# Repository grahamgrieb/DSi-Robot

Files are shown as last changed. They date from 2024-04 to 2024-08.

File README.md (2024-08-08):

#### This project uses a Nintendo DSi to control a worm-like origami robot. The  DSi also streams live video data from its webcam to a TFT Display on the robot. This project involved programming custom homebrew, designing a PCB cartridge for the DSi, wireless ESP to ESP communication, image encoding, and motor control. Both the robot and DSi operate completely wirelessly.
| *The robot and the DSi with its custom cartridge slotted in* |
|:--:|
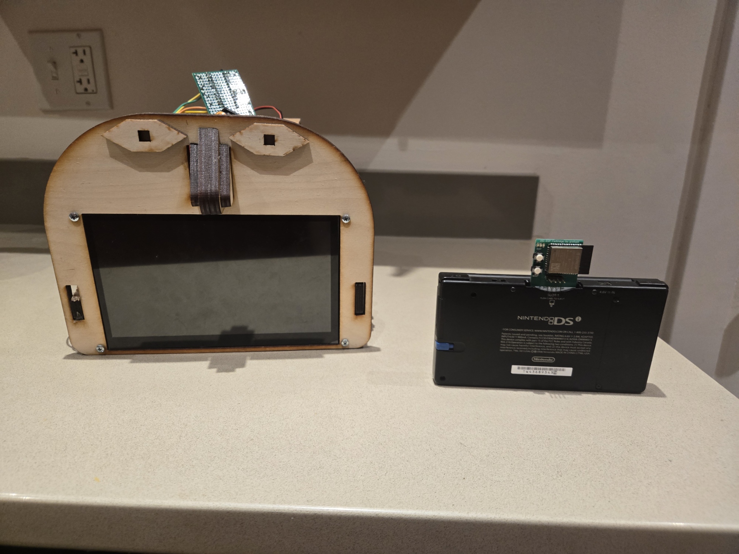
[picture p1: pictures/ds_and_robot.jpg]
Photo of DSi and Robot
|  |

| *Block Diagram overview of all the devices in the system* |
|:--:|
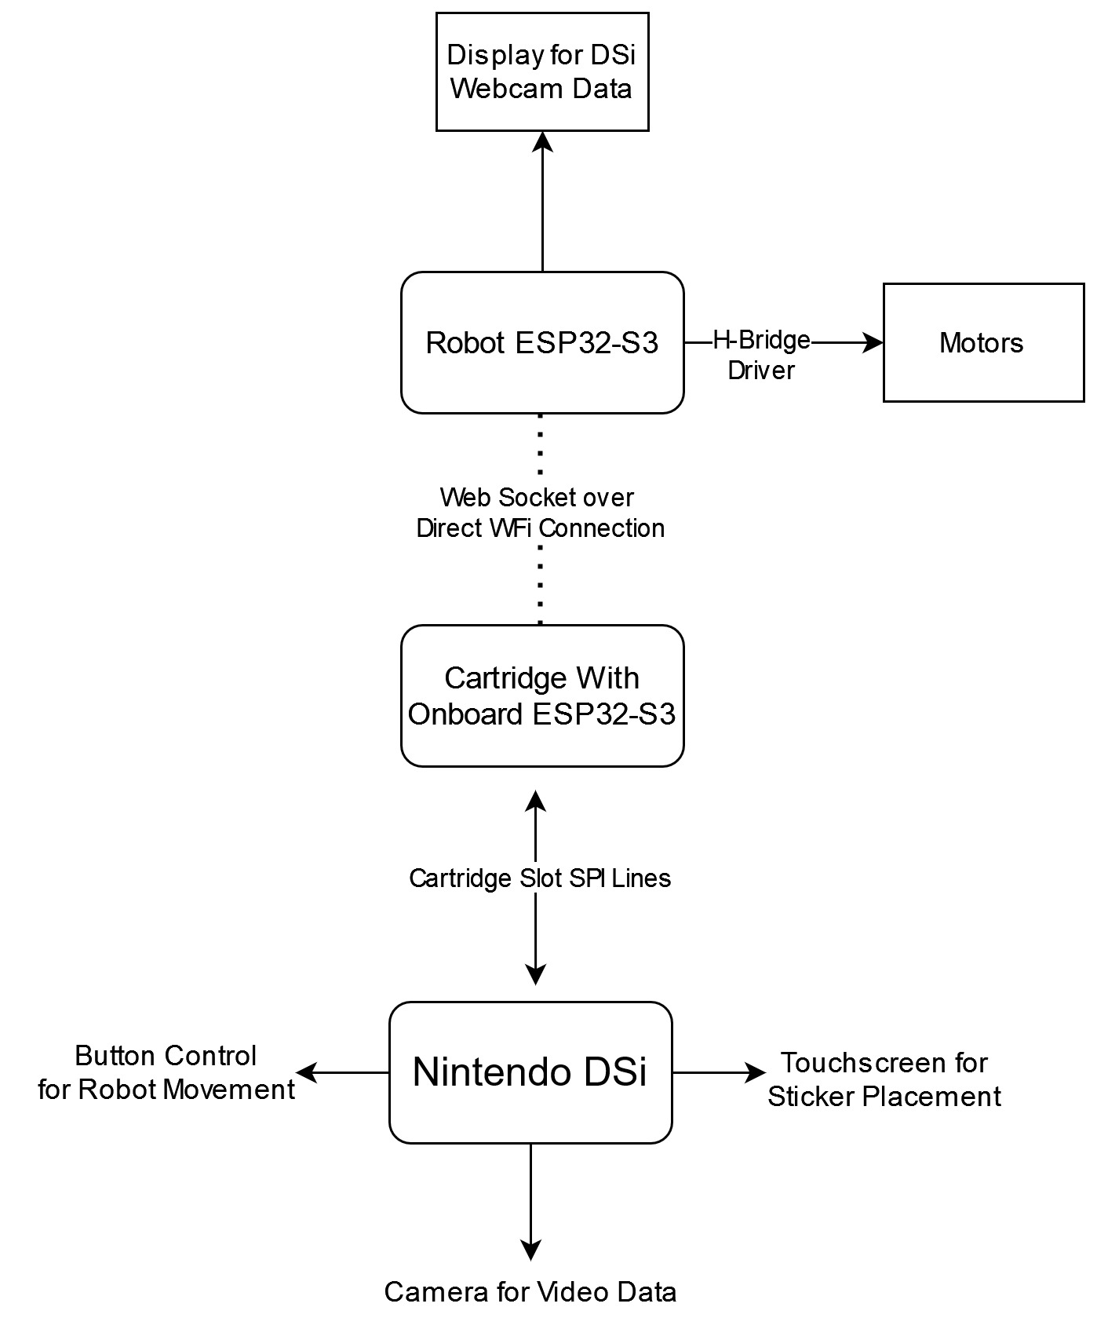
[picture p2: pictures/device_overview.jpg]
Device Block Diagram
|  |

The first part of this project is the Nintendo DSi. The DSi is running handwritten homebrew code (can be found in the **ds-app** folder). This application display the current DSi webcam data on the top screen. The user is able to place stickers over the webcam footage using the touchscreen. They are also able to switch between the front and back camera of the DSi. The webcam data is sent automatically if the user is in video mode, or whenever the user hits the A button when they are in photo mode. 

| *DSi Application with all the Stickers Placed* |
|:--:|
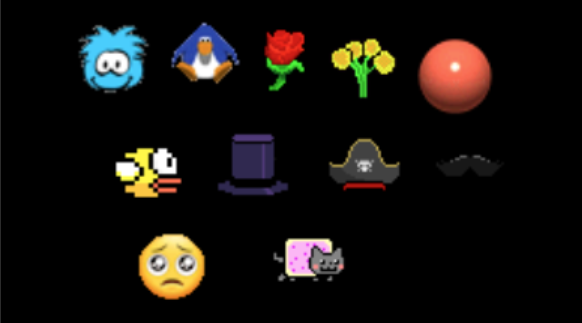
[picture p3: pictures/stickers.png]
DSi App
|  |

This application takes advantage of the two CPU's on the DSi. The image data is sent out over the SPI lines in the cartridge slot. The ARM9 CPU takes care of the main application, while the ARM7 CPU sends the SPI data in the background. These CPU's communicate with each other using the IPC register.

| *Close up of custom DSi Cartridge PCB and screenshots of Gerber files.* |
|:--:|
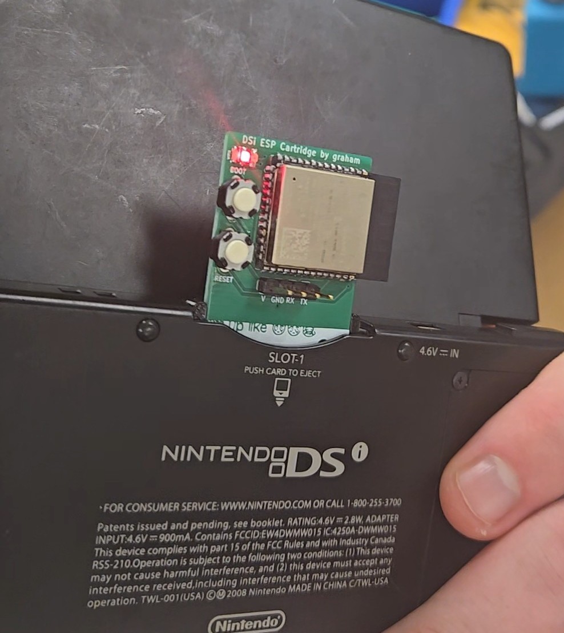
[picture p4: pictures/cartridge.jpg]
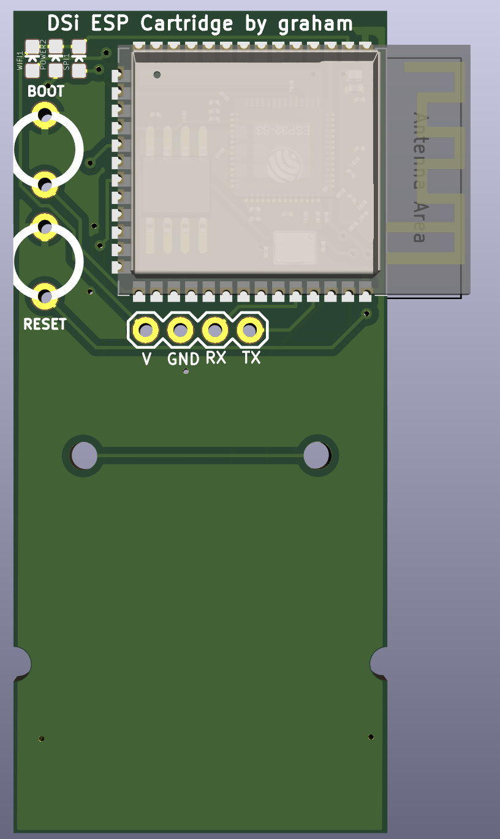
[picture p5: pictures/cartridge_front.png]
Front of Gerber
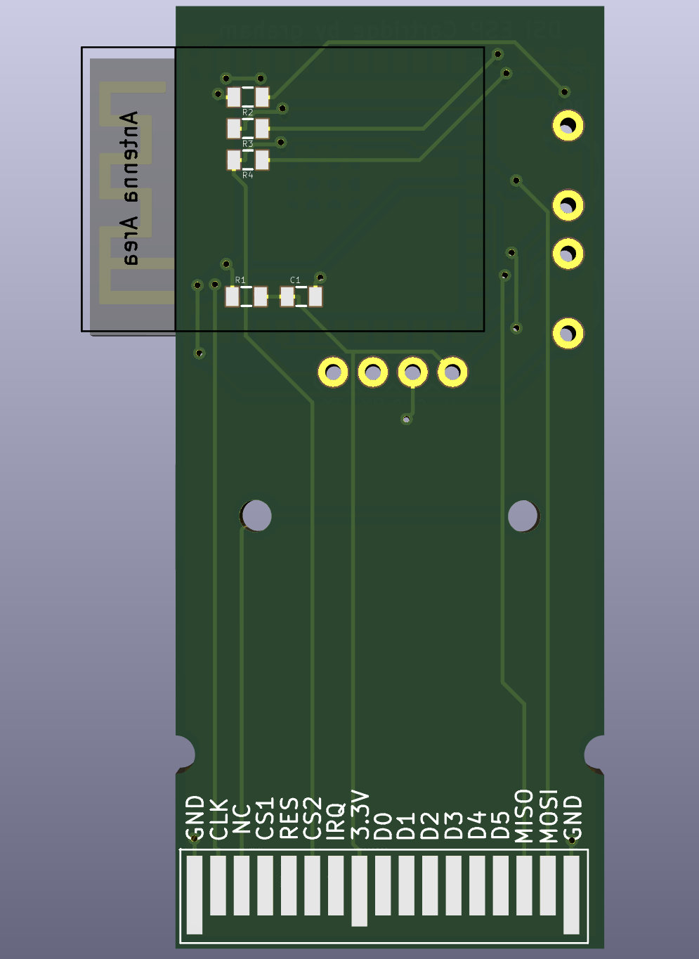
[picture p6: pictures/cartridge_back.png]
Back of Gerber
|     |

The raw bitmap image data is received over SPI on the ESP32-S3 on our custom cartridge PCB. This ESP32 is setup as SPI peripheral. It encodes the image as a JPEG (to reduce its size) and then sends it out over a WiFi WebSocket. It also receives and sends out the movement cortol signals for the robot. The code for this section can be found in **esp32-sender** folder.

The 7" TFT DIS08070H TFT Display is also powered by an ESP32-S3. The display ESP32 receives the data from the cartridge ESP32 over the direct Wifi connection. When it receives image data, it immediately draws it to the display. When it receives movement control signals, its uses our H-Bridge to appropiately tell the motors how to move. The code for this section can be found in **esp32-receiver** folder.

| *Side View of Robot* |
|:--:|
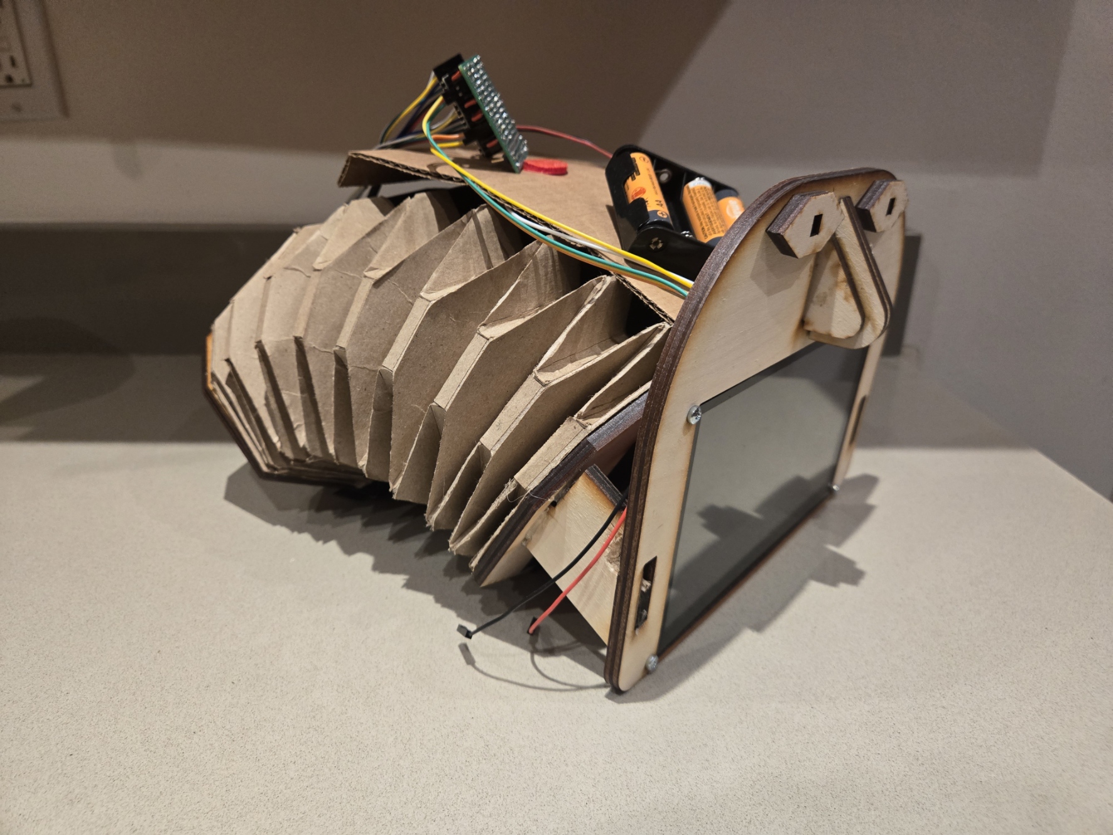
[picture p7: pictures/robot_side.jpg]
Side View of Robot
|  |

 For the robot, the design was inspired by a metamaterial soft snake robot built by the University of Southern Denmark. This design uses a Yoshimura Crease Pattern. 

The files for the cartridge PCB can be found in the **cartridge_pcb** folder and the CAD files for the cartridge housing in the **cartridge_cad** folder. The laser cutting and CAD files for the worm robot can be found in the **robot** folder.

| *Flowchart of the software/algorithm design* |
|:--:|
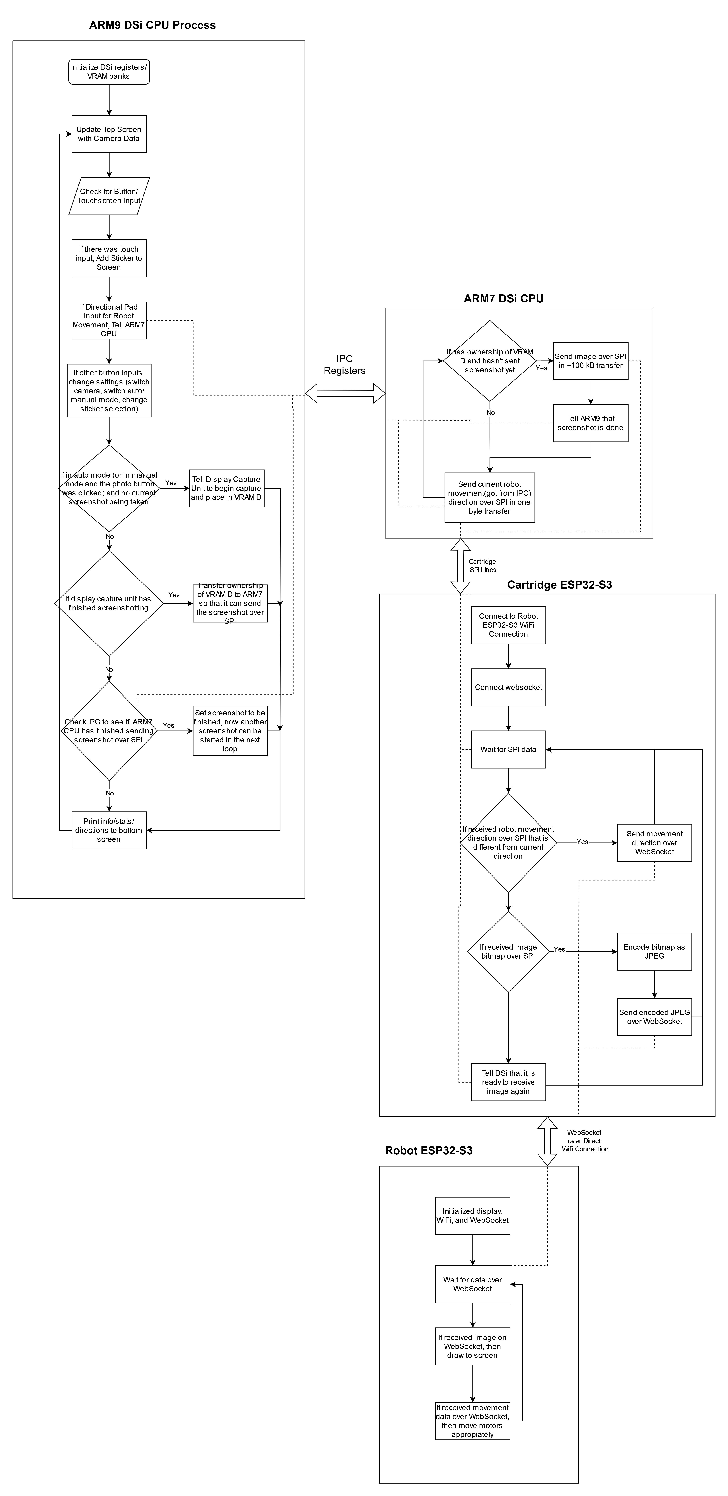
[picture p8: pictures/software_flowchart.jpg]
Software Flowchart
|  |

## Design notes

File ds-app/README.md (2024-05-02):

A homebrew application for the Nintendo DSi. Allows the user to place stickers over a live-view of the camera and save photos. Use the left and right button to change what sticker you are placing. Use b button to switch cameras.

Run make in home directory to build the program. Program cannot be run on any DSi emulators as they do not emulate the camera. devkitpro must be installed in order to build the program. The libcamera library(https://github.com/FTC55/libcamera) must also be in a parent directory to be able to build. An already built .nds file is included in the repository, this is the file that is loaded onto the DS and run.

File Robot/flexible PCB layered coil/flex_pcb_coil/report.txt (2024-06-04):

Info: Processing symbol 'J1:Connector_PinHeader_2.54mm:PinHeader_1x02_P2.54mm_Vertical'.
Added J1 (footprint 'Connector_PinHeader_2.54mm:PinHeader_1x02_P2.54mm_Vertical').
Changed REF** reference designator to J1.
Changed J1 value from PinHeader_1x02_P2.54mm_Vertical to Conn_01x02.
Updated J1 symbol association from  to /636ee8de-5b70-4620-9619-cd7a34cb071d.
Updated J1 properties.
Add net Net-(J1-Pin_1).
Connected J1 pin 1 to Net-(J1-Pin_1).
Connected J1 pin 2 to Net-(J1-Pin_1).
Warning: Via connected to unknown net ().
Warning: Via connected to unknown net ().
Warning: Via connected to unknown net ().
Warning: Via connected to unknown net ().
Warning: Via connected to unknown net ().
Warning: Via connected to unknown net ().
Warning: Via connected to unknown net ().
Warning: Via connected to unknown net ().
Warning: Via connected to unknown net ().
Warning: Via connected to unknown net ().
Warning: Via connected to unknown net ().
Warning: Via connected to unknown net ().
Warning: Via connected to unknown net ().
Warning: Via connected to unknown net ().
Warning: Via connected to unknown net ().
Warning: Via connected to unknown net ().

Info: Total warnings: 16, errors: 0.

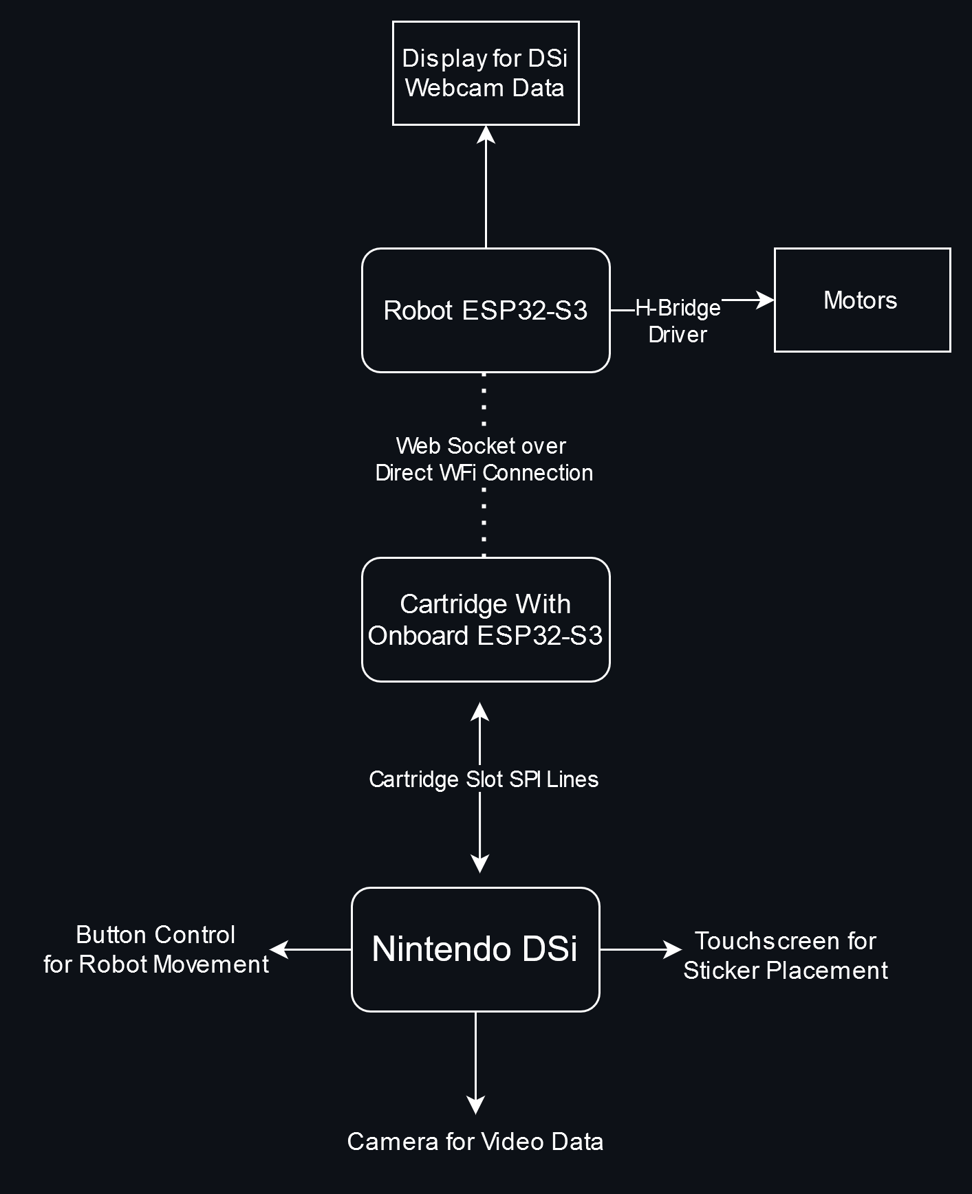
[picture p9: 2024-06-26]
pictures/device_overview.png

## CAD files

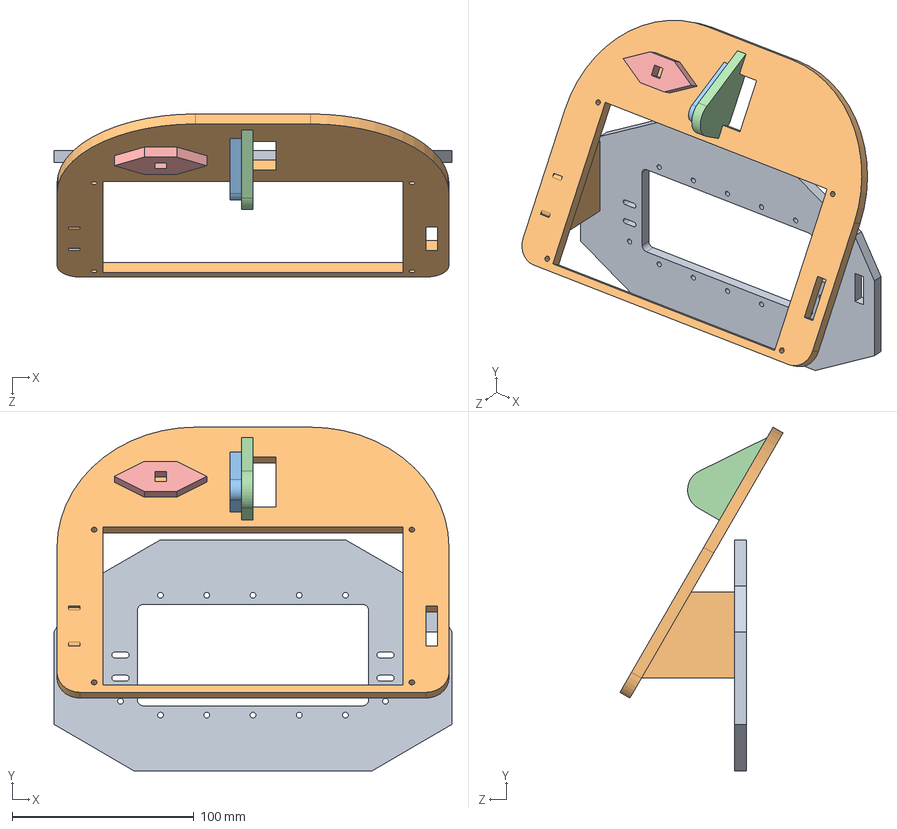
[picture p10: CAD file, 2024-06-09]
Robot/sketch_assem.SLDASM
218.7 x 188.9 x 89.6 mm
Part2^sketch_assem
Part6^sketch_assem
Part8^sketch_assem
Part9^sketch_assem
Part10^sketch_assem

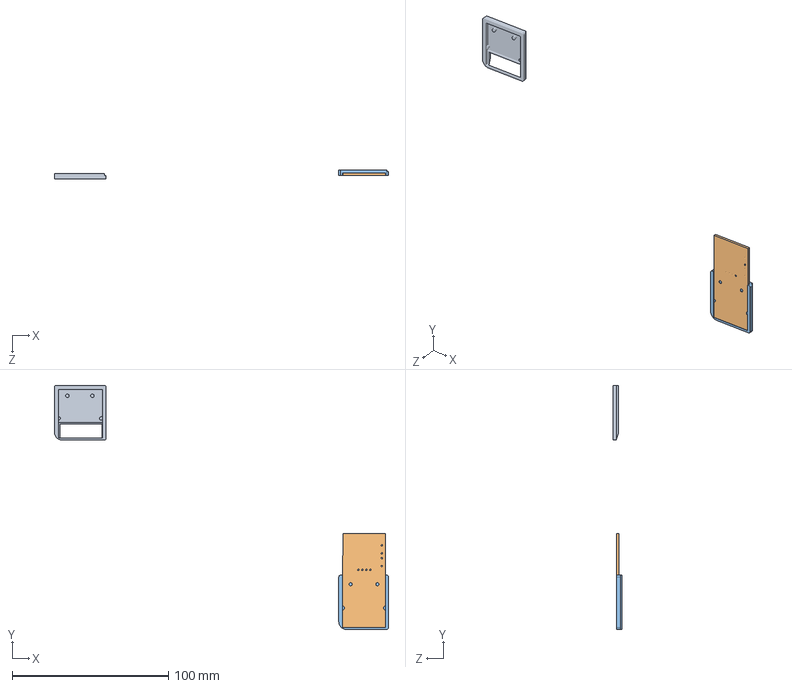
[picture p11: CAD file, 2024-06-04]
cartridge_cad/cartridge_assembly.SLDASM
213.7 x 156.2 x 5.99 mm
catridge
dsi_esp_PCB.step
print_cartridge

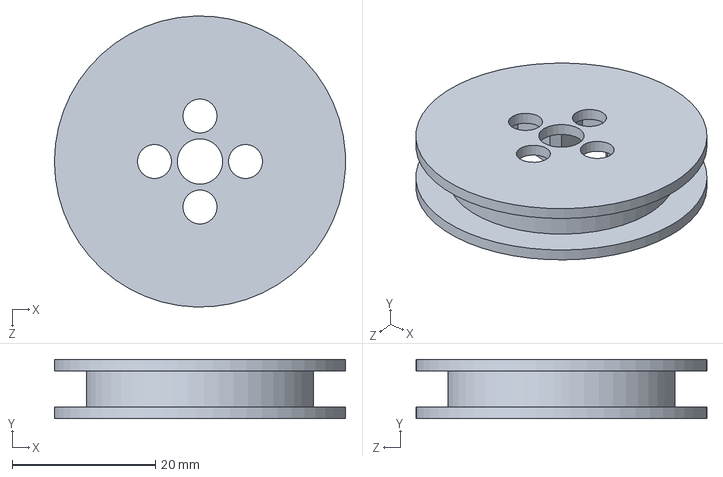
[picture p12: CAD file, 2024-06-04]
Robot/motor_mount.SLDASM
40.6 x 8.26 x 40.6 mm

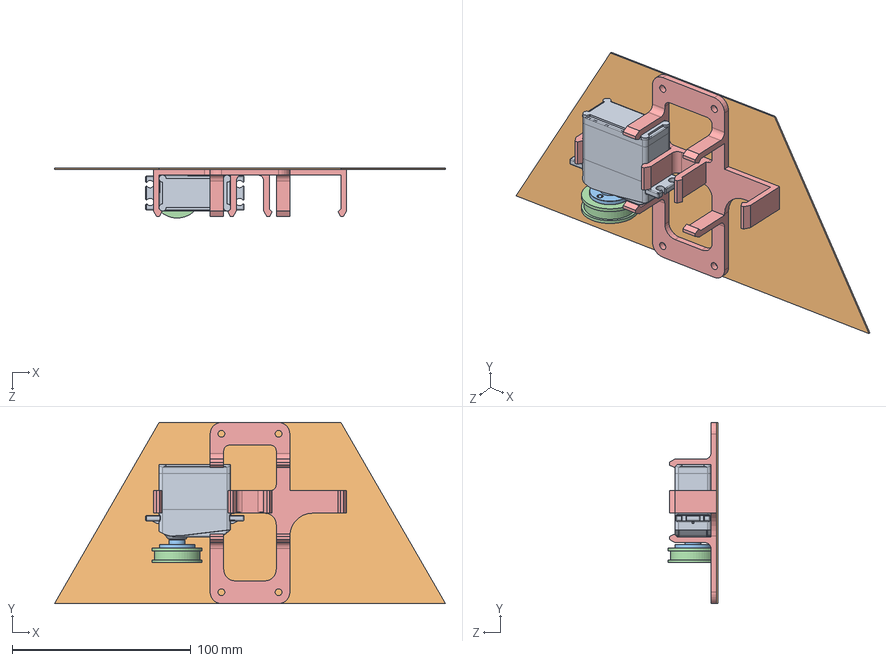
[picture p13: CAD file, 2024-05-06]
Robot/robo_cap_assembly.SLDASM
218.9 x 101.4 x 28.0 mm
LewanSoul LD-20M Servo 20kg
Part2^robo_cap_assembly
servo horn
spool
motor_holder_v1

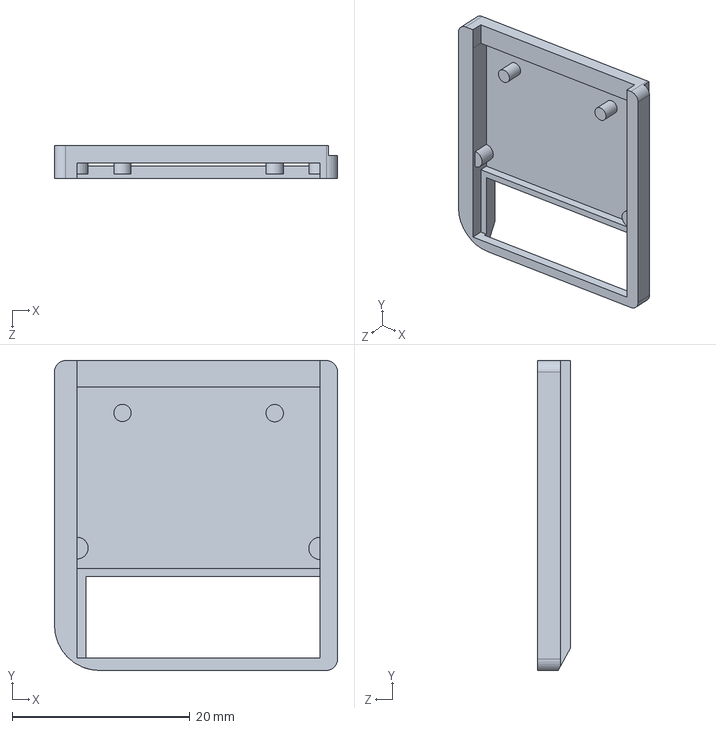
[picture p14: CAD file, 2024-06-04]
cartridge_cad/print_cartridge.SLDPRT
31.9 x 34.9 x 3.73 mm

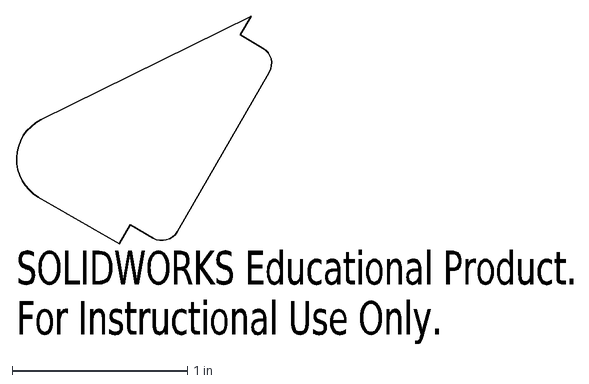
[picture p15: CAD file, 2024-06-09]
Robot/lasercut shits/nose_1.DXF
SOLIDWORKS Educational Product.
For Instructional Use Only.

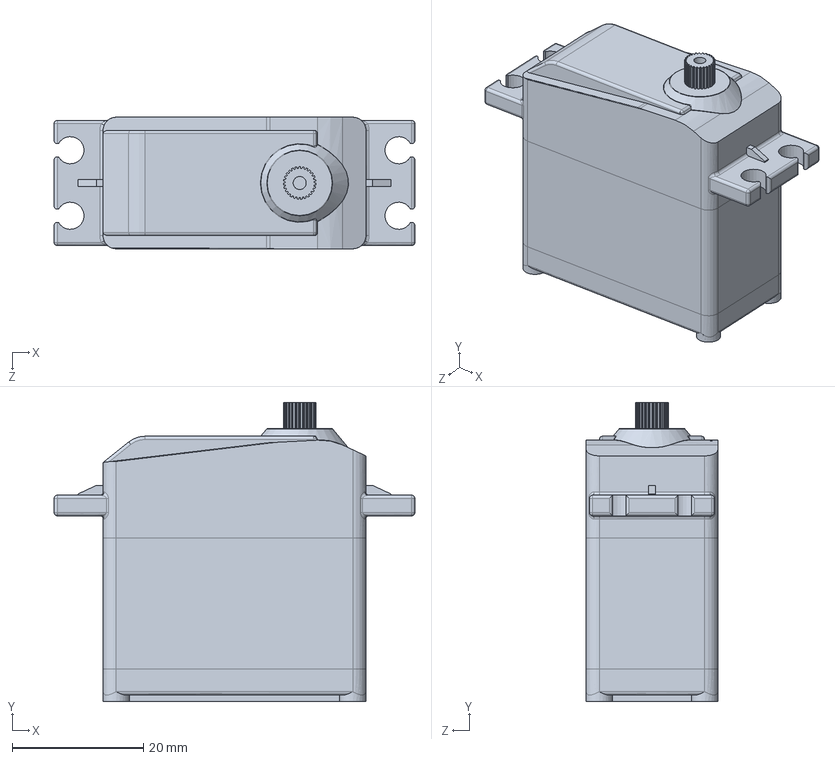
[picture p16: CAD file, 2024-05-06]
Robot/servo-motor-servo-20kg-1.snapshot.3/LewanSoul LD-20M Servo 20kg.SLDPRT
55.1 x 45.7 x 20.1 mm

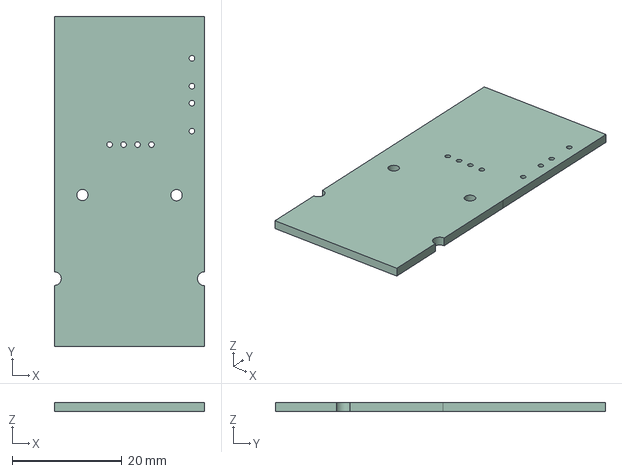
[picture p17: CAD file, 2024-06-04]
cartridge_cad/dsi_esp.step
27.3 x 60.0 x 1.60 mm

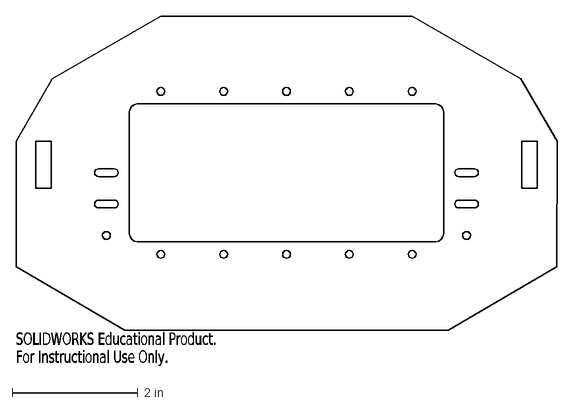
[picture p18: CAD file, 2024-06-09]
Robot/lasercut shits/front_plate.DXF
SOLIDWORKS Educational Product.
For Instructional Use Only.

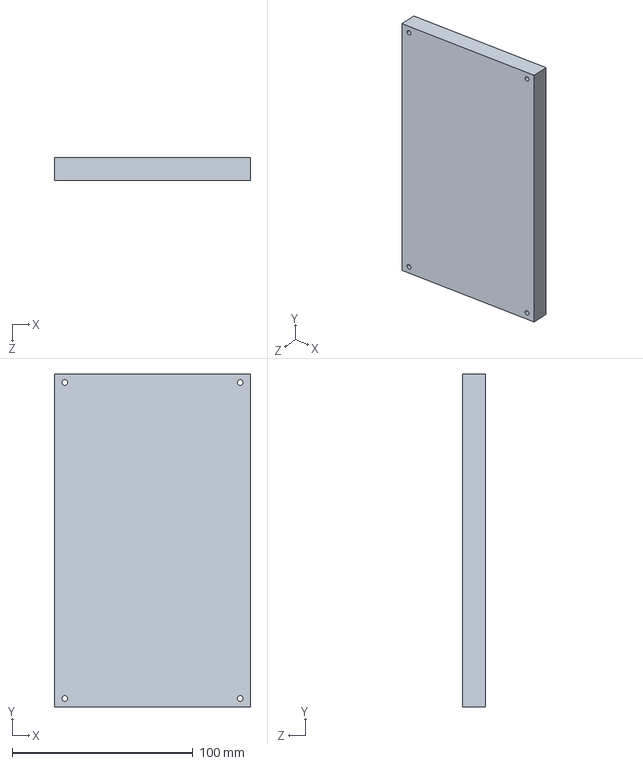
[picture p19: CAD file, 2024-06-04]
Robot/dummy_lcd.SLDPRT
108.4 x 184.0 x 12.6 mm

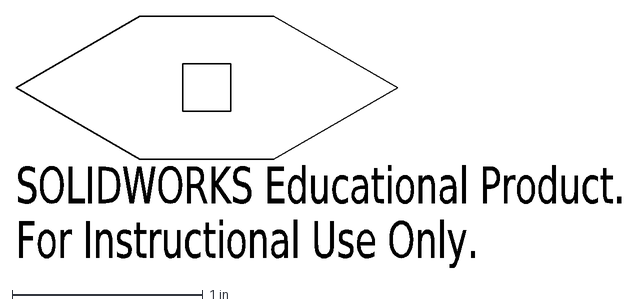
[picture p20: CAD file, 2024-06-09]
Robot/lasercut shits/eye.DXF
SOLIDWORKS Educational Product.
For Instructional Use Only.

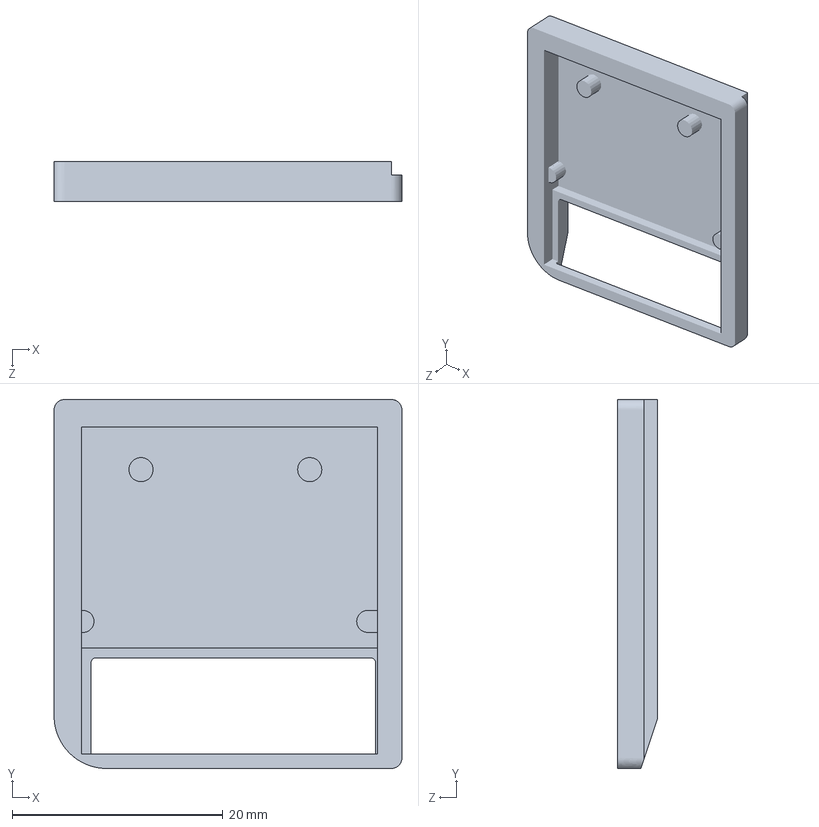
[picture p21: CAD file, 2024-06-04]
cartridge_cad/catridge.SLDPRT
33.0 x 35.0 x 3.75 mm

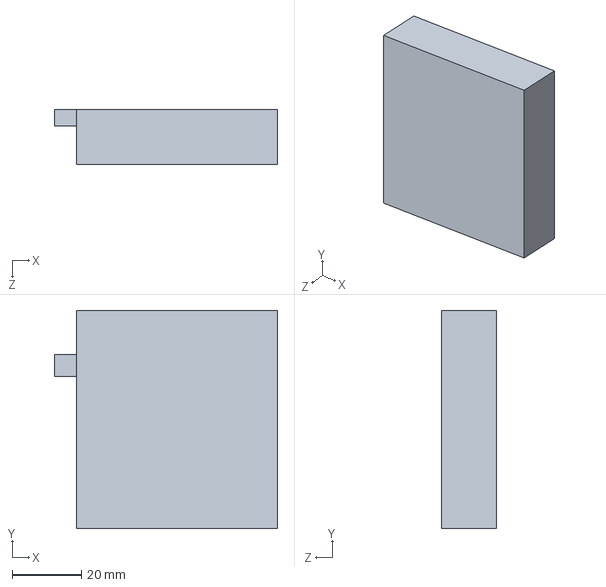
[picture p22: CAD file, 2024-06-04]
Robot/dummy_battery_pack.SLDPRT
64.3 x 63.0 x 16.0 mm

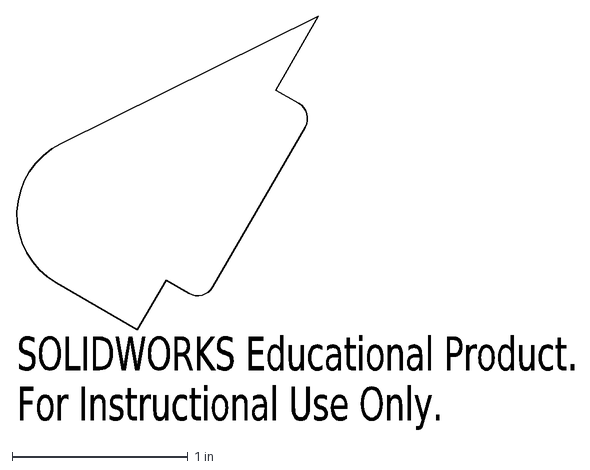
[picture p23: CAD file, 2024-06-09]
Robot/lasercut shits/nose_2.DXF
SOLIDWORKS Educational Product.
For Instructional Use Only.

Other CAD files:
Robot/robot_motor_end_cap.SLDPRT
Robot/lasercut shits/worm_body.DXF
Robot/spool.SLDPRT
Robot/lasercut shits/face_plate.DXF
Robot/lasercut shits/angler.DXF
Robot/lasercut_pattern.DXF
Robot/lasercut_pattern.SLDPRT
Robot/lasercut_pattern2.DXF
Robot/lasercut_pattern2.dxf.SLDPRT
Robot/lasercut_pattern3.DXF
Robot/motor_holder_v1.SLDPRT
Robot/motor_holder_v1.STL
Robot/motor_mount - Part1^motor_mount-2.STL
Robot/motor_mount - motor_mount_top-1.3mf
Robot/motor_mount - motor_mount_top-1.STL
Robot/motor_mount - spool-1.STL
Robot/motor_mount_top.SLDPRT
Robot/robot_battery_end_cap.DXF
Robot/robot_motor_end_cap.DXF
Robot/servo horn.SLDPRT
Robot/spool.STL
Robot/spool_v2.3mf
Robot/spool_v2.STL
cartridge_cad/dsi_esp.SLDASM
cartridge_cad/print_cartridge.3mf
cartridge_cad/print_cartridge.STL

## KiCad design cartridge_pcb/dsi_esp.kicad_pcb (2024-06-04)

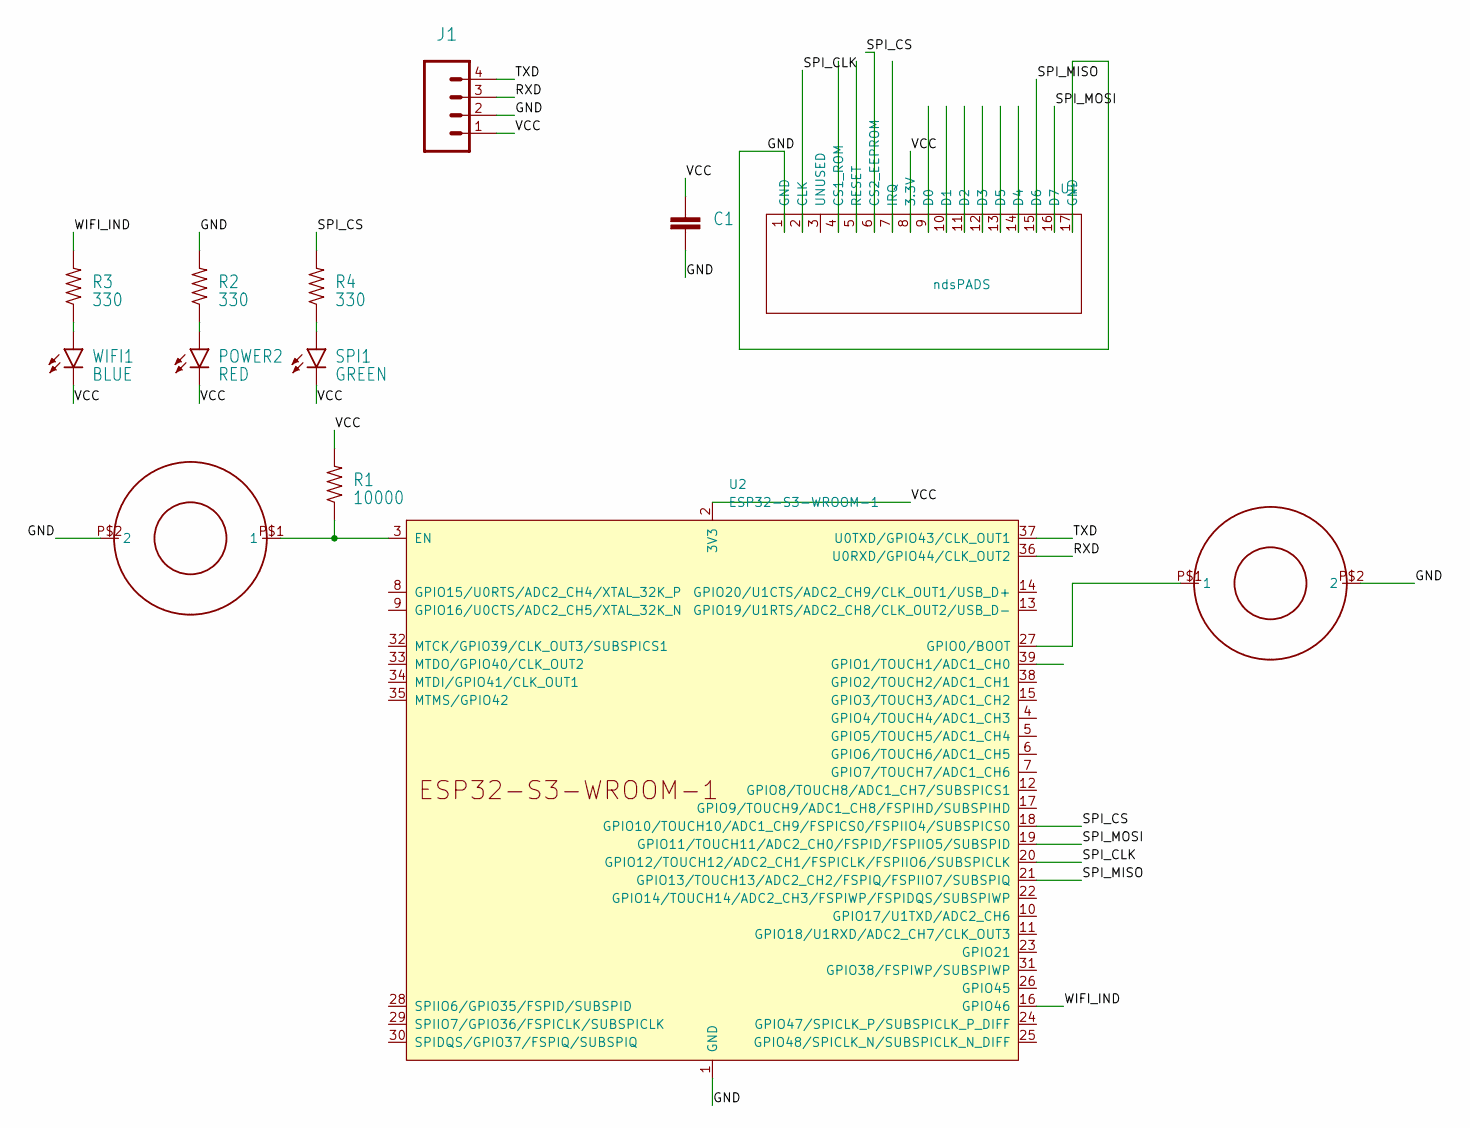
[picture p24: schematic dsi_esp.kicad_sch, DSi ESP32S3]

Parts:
BOOT1: BTN_2
C1: 0805
J1: 1X04
POWER2: RED; LED-0603
R1: 10000; 0805
R2, R3, R4: 330; 0805
RESET1: BTN_2
SPI1: GREEN; LED-0603
U1: ndsPADS; nds_contact_pads
U2: ESP32-S3-WROOM-1
WIFI1: BLUE; LED-0603

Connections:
/GND: BOOT1.P$2 (2), C1.2, J1.2, R2.2, RESET1.P$2 (2), U1.1 (GND), U1.17 (GND), U2.1 (GND), U2.40 (GND), U2.41 (GND)
/RXD: J1.3, U2.36 (U0RXD/GPIO44/CLK_OUT2)
/SPI_CLK: U1.2 (CLK), U2.20 (GPIO12/TOUCH12/ADC2_CH1/FSPICLK/FSPIIO6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)
/SPI_CS: R4.2, U1.6 (CS2_EEPROM), U2.18 (GPIO10/TOUCH10/ADC1_CH9/FSPICS0/FSPIIO4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)
/SPI_MISO: U1.15 (D6), U2.21 (GPIO13/TOUCH13/ADC2_CH2/FSPIQ/FSPIIO7/S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)
/SPI_MOSI: U1.16 (D7), U2.19 (GPIO11/TOUCH11/ADC2_CH0/FSPID/FSPIIO5/S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)
/TXD: J1.4, U2.37 (U0TXD/GPIO43/CLK_OUT1)
/VCC: C1.1, J1.1, POWER2.C, R1.2, SPI1.C, U1.8 (3.3V), U2.2 (3V3), WIFI1.C
/WIFI_IND: R3.2, U2.16 (GPIO46)
unnamed: BOOT1.P$1 (1), U2.27 (GPIO0/BOOT)
unnamed: POWER2.A, R2.1
unnamed: R3.1, WIFI1.A
unnamed: R4.1, SPI1.A
unnamed: R1.1, RESET1.P$1 (1), U2.3 (EN)

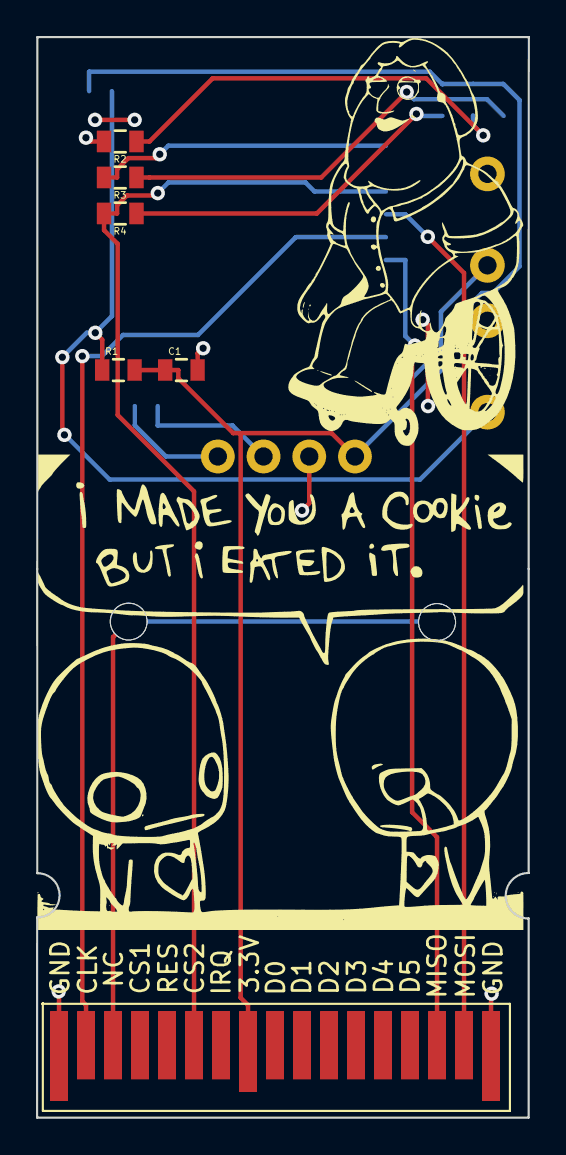
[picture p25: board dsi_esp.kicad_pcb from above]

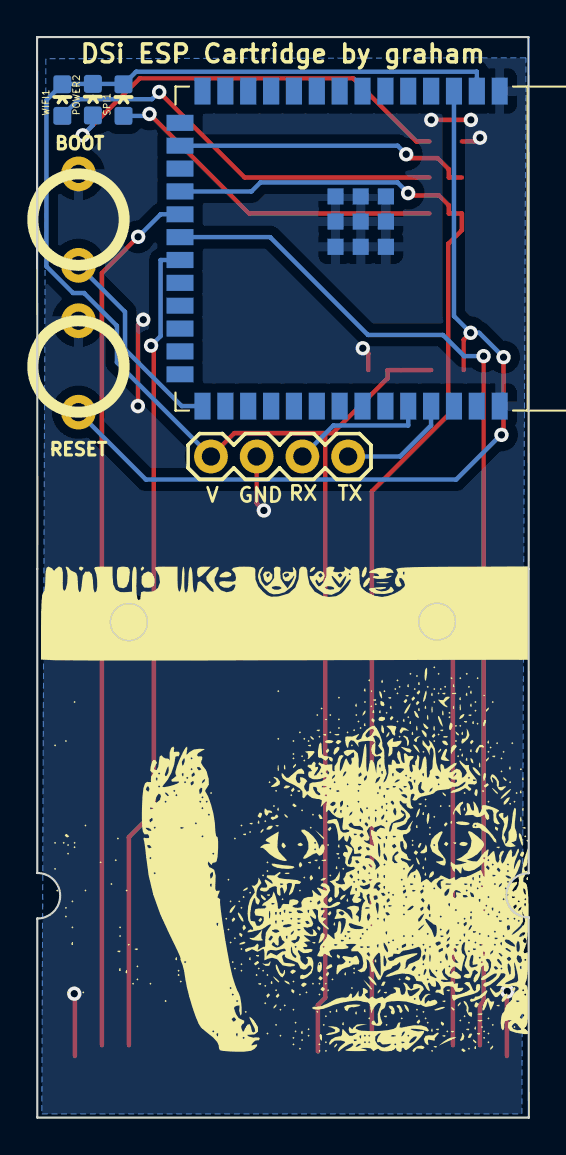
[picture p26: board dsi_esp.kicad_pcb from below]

Board: 2 copper layers, 27.3 x 60.0 mm, 16 parts (8 on the bottom side), 14 nets.

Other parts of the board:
cookie: LOGO
joe: LOGO
up: LOGO

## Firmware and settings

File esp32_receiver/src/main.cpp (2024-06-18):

#include <Arduino.h>
#include <lvgl.h>
#define LGFX_USE_V1
#include <LovyanGFX.hpp>
#include <lgfx/v1/platforms/esp32s3/Panel_RGB.hpp>
#include <lgfx/v1/platforms/esp32s3/Bus_RGB.hpp>
#include <SPIFFS.h>
#include <SPI.h>
#include <ArduinoWebsockets.h>
using namespace websockets;

#define PWM_PIN_1 19         // PWM output pin
#define DIRECTION_PIN_1 20   // Direction control pin
#define PWM_PIN_2 38         // PWM output pin
#define DIRECTION_PIN_2 44   // Direction control pin
#define PWM_FREQUENCY 100000 // 100 kHz
#define PWM_RESOLUTION 8     // 8-bit resolution
#define PWM_CHANNEL_1 0      // PWM channel
#define PWM_CHANNEL_2 2      // PWM channel
#define SWITCH_INTERVAL 5000 // Interval to change direction in milliseconds
int direction = HIGH;        // Initial direction state

WebsocketsClient client;
// Set your access point network credentials
const char *ssid = "Graham-ESP32";
const char *password = "123456789";

uint8_t movement = 4;
TaskHandle_t Task1;

SPIClass &spi = SPI;

int i = 0;
// #include <Arduino_GFX_Library.h>
#define TFT_BL 2
// Define a class named LGFX, inheriting from the LGFX_Device class.
class LGFX : public lgfx::LGFX_Device
{
public:
  // Instances for the RGB bus and panel.
  lgfx::Bus_RGB _bus_instance;
  lgfx::Panel_RGB _panel_instance;

  // Constructor for the LGFX class.
  LGFX(void)
  {
    // Configure the RGB bus.
    {
      auto cfg = _bus_instance.config();
      cfg.panel = &_panel_instance;

      // Configure data pins.
      cfg.pin_d0 = GPIO_NUM_15; // B0
      cfg.pin_d1 = GPIO_NUM_7;  // B1
      cfg.pin_d2 = GPIO_NUM_6;  // B2
      cfg.pin_d3 = GPIO_NUM_5;  // B3
      cfg.pin_d4 = GPIO_NUM_4;  // B4

      cfg.pin_d5 = GPIO_NUM_9;  // G0
      cfg.pin_d6 = GPIO_NUM_46; // G1
      cfg.pin_d7 = GPIO_NUM_3;  // G2
      cfg.pin_d8 = GPIO_NUM_8;  // G3
      cfg.pin_d9 = GPIO_NUM_16; // G4
      cfg.pin_d10 = GPIO_NUM_1; // G5

      cfg.pin_d11 = GPIO_NUM_14; // R0
      cfg.pin_d12 = GPIO_NUM_21; // R1
      cfg.pin_d13 = GPIO_NUM_47; // R2
      cfg.pin_d14 = GPIO_NUM_48; // R3
      cfg.pin_d15 = GPIO_NUM_45; // R4

      // Configure sync and clock pins.
      cfg.pin_henable = GPIO_NUM_41;
      cfg.pin_vsync = GPIO_NUM_40;
      cfg.pin_hsync = GPIO_NUM_39;
      cfg.pin_pclk = GPIO_NUM_0;
      cfg.freq_write = 15000000;

      // Configure timing parameters for horizontal and vertical sync.
      cfg.hsync_polarity = 0;
      cfg.hsync_front_porch = 40;
      cfg.hsync_pulse_width = 48;
      cfg.hsync_back_porch = 40;

      cfg.vsync_polarity = 0;
      cfg.vsync_front_porch = 1;
      cfg.vsync_pulse_width = 31;
      cfg.vsync_back_porch = 13;

      // Configure polarity for clock and data transmission.
      cfg.pclk_active_neg = 1;
      cfg.de_idle_high = 0;
      cfg.pclk_idle_high = 0;

      // Apply configuration to the RGB bus instance.
      _bus_instance.config(cfg);
    }

    // Configure the panel.
    {
      auto cfg = _panel_instance.config();
      cfg.memory_width = 800;
      cfg.memory_height = 480;
      cfg.panel_width = 800;
      cfg.panel_height = 480;
      cfg.offset_x = 0;
      cfg.offset_y = 0;

      // Apply configuration to the panel instance.
      _panel_instance.config(cfg);
    }

    // Set the RGB bus and panel instances.
    _panel_instance.setBus(&_bus_instance);
    setPanel(&_panel_instance);
  }
};

LGFX lcd;

// on receive data over WebSocket
void onMessageCallback(WebsocketsMessage message)
{
  Serial.printf("Received %d bytes\n", message.length());

  // received movement direction
  if (message.length() == 1)
  {
    Serial.printf("New Direction: %x\n", message.rawData().data()[0]);
    movement = message.rawData().data()[0];
    return;
  }
  // received JPG image
  else
  {
    auto data = message.rawData().data();
    if (!(data[0] == 0xFF && data[1] == 0xD8))
    {
      Serial.println("No JPG Header");
      return;
    };

    unsigned long timer = millis();
    // draw JPG
    if (!lcd.drawJpg((uint8_t *)data, message.length(), 80, 0, 256, 192))
    {
      Serial.println("Error drawing jpg");
    }
    Serial.printf("Draw time: %d\n", millis() - timer);

    Serial.println("Drew JPG");
  }
}

void onEventsCallback(WebsocketsEvent event, String data)
{
  if (event == WebsocketsEvent::ConnectionOpened)
  {
    Serial.println("Connnection Opened");
  }
  else if (event == WebsocketsEvent::ConnectionClosed)
  {
    Serial.println("Connnection Closed");
  }
  else if (event == WebsocketsEvent::GotPing)
  {
    Serial.println("Got a Ping!");
  }
  else if (event == WebsocketsEvent::GotPong)
  {
    Serial.println("Got a Pong!");
  }
}

/* Display flushing */
void my_disp_flush(lv_disp_drv_t *disp, const lv_area_t *area, lv_color_t *color_p)
{

  uint32_t w = (area->x2 - area->x1 + 1);
  uint32_t h = (area->y2 - area->y1 + 1);

  // lcd.fillScreen(TFT_WHITE);
#if (LV_COLOR_16_SWAP != 0)
  lcd.pushImageDMA(area->x1, area->y1, w, h, (lgfx::rgb565_t *)&color_p->full);
#else
  lcd.pushImageDMA(area->x1, area->y1, w, h, (lgfx::rgb565_t *)&color_p->full); //
#endif

  lv_disp_flush_ready(disp);
}
// motor control loop running asynchronously on core 0
void Task1code(void *pvParameters)
{
  for (;;)
  {
    // forward movement
    if (movement == 1)
    {
      direction = LOW;
      ledcWrite(PWM_CHANNEL_1, 255);
      ledcWrite(PWM_CHANNEL_2, 255); // dir low
      // contract
      digitalWrite(DIRECTION_PIN_1, direction);  // low makes right motor turn cw
      digitalWrite(DIRECTION_PIN_2, !direction); // high makes left motor turn ccw
      delay(1000);
      // expand
      direction = !direction;
      digitalWrite(DIRECTION_PIN_1, direction);
      digitalWrite(DIRECTION_PIN_2, !direction);
      delay(300);
    }
    // left movement
    else if (movement == 2)
    {
      direction = LOW;
      ledcWrite(PWM_CHANNEL_1, 255);
      ledcWrite(PWM_CHANNEL_2, 200); // dir low
      // contract
      digitalWrite(DIRECTION_PIN_1, direction);  // low makes right motor turn cw
      digitalWrite(DIRECTION_PIN_2, !direction); // high makes left motor turn ccw
      delay(1000);
      // expand
      direction = !direction;
      digitalWrite(DIRECTION_PIN_1, direction);
      digitalWrite(DIRECTION_PIN_2, !direction);
      delay(300);
    }
    // right movement
    else if (movement == 3)
    {
      direction = LOW;
      ledcWrite(PWM_CHANNEL_1, 200);
      ledcWrite(PWM_CHANNEL_2, 255); // dir low
      // contract
      digitalWrite(DIRECTION_PIN_1, direction);  // low makes right motor turn cw
      digitalWrite(DIRECTION_PIN_2, !direction); // high makes left motor turn ccw
      delay(1000);
      // expand
      direction = !direction;
      digitalWrite(DIRECTION_PIN_1, direction);
      digitalWrite(DIRECTION_PIN_2, !direction);
      delay(300);
    }
    //stop movement
    else if (movement == 4)
    {
      ledcWrite(PWM_CHANNEL_1, 0);
      ledcWrite(PWM_CHANNEL_2, 0);
    }
  }
}

void setup()
{
  Serial.begin(115200);
  if (!SPIFFS.begin())
  {
    Serial.println("An Error has occurred while mounting SPIFFS");
    return;
  }
  if (!psramInit())
  {
    Serial.println("PSRAM FAIL");
  }
  // host WiFi network
  WiFi.softAP(ssid, password);

  IPAddress IP = WiFi.softAPIP();
  Serial.printf("IP address: %s\n", IP.toString().c_str());

  client.onMessage(onMessageCallback);
  client.onEvent(onEventsCallback);

  // init LCD
  lcd.init();
  lcd.setColorDepth(24);
  lcd.setTextSize(2);
  delay(200);
  // turn on backlight
  pinMode(TFT_BL, OUTPUT);
  digitalWrite(TFT_BL, HIGH);

  Serial.println("init done");

  // draw borders
  File border = SPIFFS.open("/heart_border.png", "r");
  lcd.drawPng(&border, 0, 0, 80, 480);
  border.close();
  delay(1000);
  File border1 = SPIFFS.open("/heart_border.png", "r");
  lcd.drawPng(&border1, 720, 0, 80, 480);
  border.close();

  // motor setup
  // Initialize the PWM pin and channel
  ledcSetup(PWM_CHANNEL_1, PWM_FREQUENCY, PWM_RESOLUTION);
  ledcSetup(PWM_CHANNEL_2, PWM_FREQUENCY, PWM_RESOLUTION);
  ledcAttachPin(PWM_PIN_1, PWM_CHANNEL_1);
  ledcAttachPin(PWM_PIN_2, PWM_CHANNEL_2);

  // Start the PWM with 50% duty cycle
  ledcWrite(PWM_CHANNEL_1, 255); // 50% of 255 (8-bit resolution)
  ledcWrite(PWM_CHANNEL_2, 255);

  // Initialize the direction pin
  pinMode(DIRECTION_PIN_1, OUTPUT);
  digitalWrite(DIRECTION_PIN_1, direction);
  pinMode(DIRECTION_PIN_2, OUTPUT);
  digitalWrite(DIRECTION_PIN_2, direction);

  // create async task for motor
  xTaskCreatePinnedToCore(
      Task1code, /* Task function. */
      "Task1",   /* name of task. */
      10000,     /* Stack size of task */
      NULL,      /* parameter of the task */
      0,         /* priority of the task */
      &Task1,    /* Task handle to keep track of created task */
      0);        /* pin task to core 0 */
}
// runs on Core 1
void loop()
{
  while (WiFi.softAPgetStationNum() < 1)
  {
    Serial.println("Waiting for WiFi connection");
    delay(1000);
  }
  if (!client.available())
  {
    Serial.println("Waiting for client");
    client.connect("192.168.4.2", 81, "/");
  }
  client.poll();
}

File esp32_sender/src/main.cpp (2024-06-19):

#include <Wire.h>
#include <SPIFFS.h> // Add this line to include the SPIFFS library
#include <ESP32DMASPISlave.h>
#include <WiFi.h>
#include <ESPNowCam.h>
#include <JPEGENC.h>
#include <ArduinoWebsockets.h>
using namespace websockets;
JPEGENC jpg;
JPEGENCODE jpe;
ESP32DMASPI::Slave slave;

#define send_size 30000
static constexpr size_t BUFFER_SIZE = 33000;
static constexpr size_t QUEUE_SIZE = 4;
uint8_t *bmp_buf1;
uint8_t *bmp_buf2;
uint8_t *bmp_buf3;
uint8_t *bmp_buf4;
uint8_t movement = 4;
// Set your access point network credentials
const char *ssid = "Graham-ESP32";
const char *password = "123456789";

WebsocketsServer server;
WebsocketsClient client;
// uint8_t* fb = (uint8_t*)  malloc(send_size) ;

void loop()
{
  // set MISO to high to let DS know ESP is ready
  digitalWrite(13, HIGH);
  // wait for DS to send data
  slave.queue(NULL, bmp_buf4, 4);
  const std::vector<size_t> received_bytes1 = slave.wait();
  // if not start of data, return
  if (received_bytes1[0] != 2 && (bmp_buf4[0] != 0x44 || bmp_buf4[0] != 0x33))
  {
    return;
  }
  // if movement changed, send movement to over wifi
  if (bmp_buf4[1] != movement)
  {
    movement = bmp_buf4[1];
    Serial.println("Movement changed");
    while (!client.available())
    {
      client = server.accept();
    }
    client.send((char *)&bmp_buf4[1], 1);
  }
  // first byte is 0x33 which means it was just sending a direction, therefore return
  if (bmp_buf4[0] != 0x44)
  {
    return;
  }
  // receive full image
  unsigned long startTime = millis();
  slave.queue(NULL, bmp_buf4, 4);
  const std::vector<size_t> received_bytes2 = slave.wait();
  if (received_bytes2[0] != 1)
  {
    return;
  }
  if (bmp_buf4[0] != 0x12)
  {
    return;
  }
  // tell DS not to send any more data
  digitalWrite(13, LOW);
  // wait for image data
  Serial.println("Waiting for data");
  slave.queue(NULL, bmp_buf1, BUFFER_SIZE);
  slave.queue(NULL, bmp_buf2, BUFFER_SIZE);
  slave.queue(NULL, bmp_buf3, BUFFER_SIZE);
  slave.queue(NULL, bmp_buf4, 4);

  const std::vector<size_t> received_bytes = slave.wait();

  if (received_bytes[0] != 32767 || received_bytes[1] != 32767 || received_bytes[2] != 32767 || received_bytes[3] != 3)
  {
    Serial.printf("Not BMP: %d %d %d %d\n", received_bytes[0], received_bytes[1], received_bytes[2], received_bytes[3]);
    return;
  }
  Serial.println("Received BMP");
  Serial.printf("SPI Time: %lu ms\n", millis() - startTime);

  // encode image as JPEG
  startTime = millis();
  uint8_t *bitmap = (uint8_t *)ps_calloc(98304, sizeof(uint8_t));
  // copy four buffers to bitmap buffers

  memcpy(bitmap, bmp_buf1, received_bytes[0]);
  memcpy(bitmap + received_bytes[0], bmp_buf2, received_bytes[1]);
  memcpy(bitmap + received_bytes[0] + received_bytes[1], bmp_buf3, received_bytes[2]);
  memcpy(bitmap + received_bytes[0] + received_bytes[1] + received_bytes[2], bmp_buf4, 3);

  // create 25k buffer
  uint8_t *jpg_buffer = (uint8_t *)ps_calloc(25000, sizeof(uint8_t));

  jpg.open(jpg_buffer, 25000);
  const int iWidth = 256, iHeight = 192;
  const int iBpp = 2;               // 24 bit color
  const int iPitch = iWidth * iBpp; // bytes per row

  int rc = jpg.encodeBegin(&jpe, iWidth, iHeight, JPEGE_PIXEL_RGB565, JPEGE_SUBSAMPLE_444, JPEGE_Q_BEST);
  int iDataSize;

  rc = jpg.addFrame(&jpe, bitmap, iPitch);
  if (rc != 0)
  {
    Serial.println("Error encoding");
  }
  // done encoding
  iDataSize = jpg.close();
  free(bitmap);
  Serial.print("Output file size = ");
  Serial.println(iDataSize, DEC);
  Serial.printf("Encoding Time: %lu ms\n", millis() - startTime);

  // send image over WiFi WebSocket

  startTime = millis();
  while (!client.available())
  {
    client = server.accept();
  }
  client.send((char *)jpg_buffer, iDataSize);

  free(jpg_buffer);
  Serial.printf("Send Time: %lu ms\n", millis() - startTime);
}

void setup()
{
  Serial.begin(9600);
  Serial.println("ESP32-S3 DSi");
  // pin 46 is BLUE LED that is on during Setup and off when done
  pinMode(46, OUTPUT);
  digitalWrite(46, LOW);
  if (!psramInit())
  {
    Serial.println("PSRAM FAIL");
    while (1)
    {
      ;
    }
  }
  // wifi code
  WiFi.begin(ssid, password);
  // Wait some time to connect to host ESP wifi
  for (int i = 0; i < 10 && WiFi.status() != WL_CONNECTED; i++)
  {
    Serial.print(".");
    delay(1000);
  }
  Serial.println("Connected to wifi");
  // Check if connected to wifi
  if (WiFi.status() != WL_CONNECTED)
  {
    Serial.println("No Wifi!");
    return;
  }
  Serial.println("Connected to WiFi");
  server.listen(81);
  Serial.print("Is server live? ");
  Serial.println(server.available());

  client = server.accept();
  Serial.println("Done connecting");

  // pin 13 is used to tell DS that ESP is ready to receive data
  pinMode(13, OUTPUT);
  digitalWrite(13, LOW);

  // SPI peripheral init code
  bmp_buf1 = slave.allocDMABuffer(BUFFER_SIZE);
  bmp_buf2 = slave.allocDMABuffer(BUFFER_SIZE);
  bmp_buf3 = slave.allocDMABuffer(BUFFER_SIZE);
  bmp_buf4 = slave.allocDMABuffer(4);

  slave.setDataMode(SPI_MODE3);          // default: SPI_MODE0
  slave.setMaxTransferSize(BUFFER_SIZE); // default: 4092 bytes
  slave.setQueueSize(QUEUE_SIZE);        // default: 1, requres 2 in this example

  slave.begin(HSPI); // default: HSPI (please refer README for pin assignments)
  Serial.println("SPI Slave initiatalized");

  pinMode(13, OUTPUT);
  digitalWrite(13, LOW);
  digitalWrite(46, HIGH);
  Serial.println("Setup complete");
}

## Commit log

2024-04-23 kicad files
    [ESP PCB.kicad_pcb, ESP PCB.kicad_sch]
2024-05-06 got display data sending over spi
2024-05-07 vram c to vram d to fix bottom screen glitch
    [arm9.cpp]
2024-05-11 flex coil
    [flex_pcb_coil-B_Cu.gbr, flex_pcb_coil-B_Mask.gbr, flex_pcb_coil-B_Paste.gbr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]
2024-05-15 added in bunch of updates for esp32 receiver and sender
2024-05-20 added dsi esp32 pcb
    [dsi_esp-B_Cu.gbl, dsi_esp-B_Mask.gbs, dsi_esp-B_Paste.gbp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]
2024-06-01 ds app updates: started using arm7 cpu to send spi messages so that rest of app doesn't freeze during send
    [arm7.c, arm9.cpp]
2024-06-02 working prototype that sends the images automatically over esp-now and is able to display. esp-now is too slow however so we need to switch from it
    [dsi_esp-B_Cu.gbl, dsi_esp-B_Mask.gbs, dsi_esp-B_Paste.gbp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]
2024-06-05 Insanely large amount of updates: switched to websockets to greatly improve fps, added new stickers, improvements in all parts of the project
2024-06-05 added motor control logic
2024-06-05 move funcs
    [sketch_assem.SLDASM]
2024-06-18 separated cad and pcb folders
    [cartridge_assembly.SLDASM, catridge.SLDPRT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]
